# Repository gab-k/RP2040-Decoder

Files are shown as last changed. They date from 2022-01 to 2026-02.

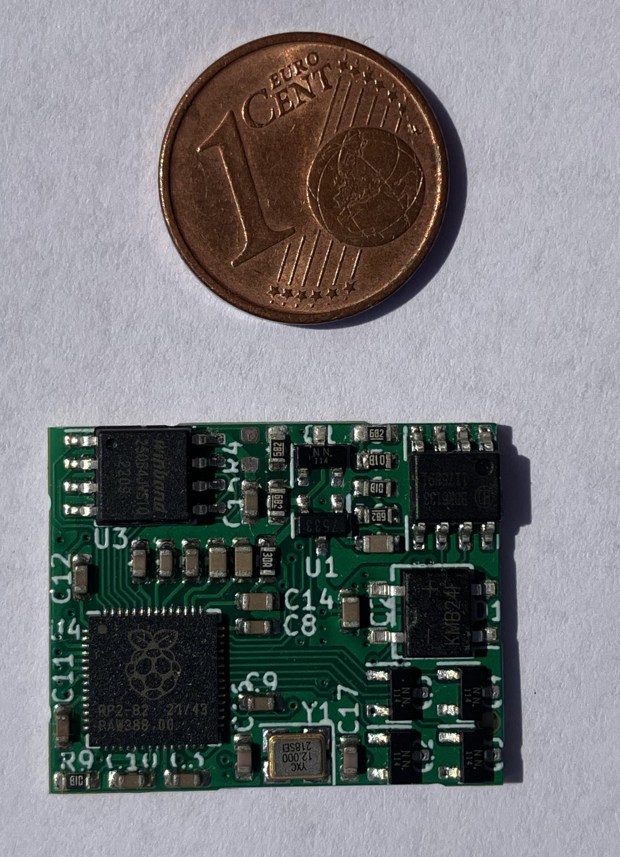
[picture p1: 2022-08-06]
docs/png/Comparison.jpg

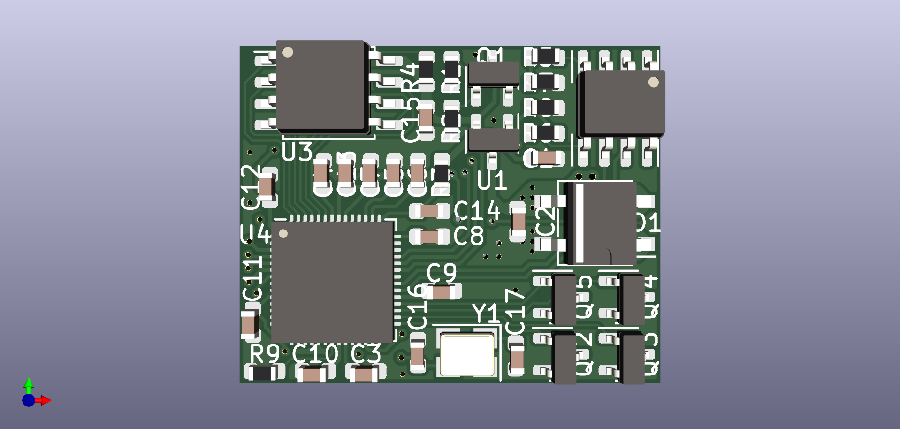
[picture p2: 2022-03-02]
docs/png/RP2040-Decoder-Rev_0_2_front.png

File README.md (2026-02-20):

# RP2040-Decoder

Designed to be a low-cost, open-source alternative to commercial DCC decoders, it utilizes the Raspberry Pi RP2040 dual-core microcontroller. The decoder features DCC protocol decoding and command interpretation alongside motor control in a compact 25x20 mm form factor.

## Key Features
*   **DCC Signal Decoding**: Interrupt-based edge detection with full packet/protocol decoding.
*   **Motor Control**: 128 speed steps with configurable acceleration/deceleration ramping and v_min/v_mid/v_max; closed-loop control for consistent motor speed under varying load conditions.
*   **Flexible I/O**: 4x transistor-switched outputs and 6x additional GPIOs; all of them PWM capable.
*   **CV Configuration**: Function mapping and programming track support.
*   **Standards Compliance**: Implements the most important NMRA (S-9.1, S-9.2.x) and RCN (210, 212, 216) DCC standards.
*   **Compact Form Factor**: 25x20 mm board size.
*   **Integrated Documentation**: Comprehensive [GitHub Pages documentation](https://gab-k.github.io/RP2040-Decoder/) covering hardware theory and software implementation.

## Architecture Overview
The system uses each of the two ARM Cortex-M0+ cores for separate tasks:

*   **Core 0: Signal Processing & Management**
    *   DCC edge detection and packet decoding.
    *   Configuration Variable (CV) management using persistent flash storage.
    *   Service Mode (Programming Track) logic and acknowledgment pulse generation.
*   **Core 1: Motion Control**
    *   **PID Controller**: A discrete-time PID motor controller implementation utilizing based on a bilinear transform formula.
    *   **Back-EMF Feedback**: ADC sampling during PWM-off cycles.
    *   **Adaptive Control**: Gain scheduling for $K_P$ and a startup controller (feed-forward) to overcome static friction.

## Hardware Revisions

### USB Version
Optimized for ease of use; supports UF2 drag-and-drop flashing and serial logging.
<div style="display: flex; gap: 10px;">
  
  
</div>

### Legacy Version
Revision without USB, one sided assembly, flashed via SWD.
<div style="display: flex; gap: 10px;">
  
  
</div>

## Getting Started

To get started, you will first need the hardware. The different options for acquiring a board are outlined [here](https://gab-k.github.io/RP2040-Decoder/sphinx/html/gs/getting_started.html#where-to-get-the-board).

For the software, you have a few options: you can either [build it from source](https://gab-k.github.io/RP2040-Decoder/sphinx/html/gs/getting_started.html#building-the-software) or use the ready-to-flash [binaries built by the CI pipeline](https://github.com/gab-k/RP2040-Decoder/releases) on each release. [Flashing the firmware](https://gab-k.github.io/RP2040-Decoder/sphinx/html/gs/getting_started.html#flashing-the-software) can be done via SWD or, if you are using the USB hardware version, simply by dragging and dropping the file using your regular file explorer.

## License

*   **Software**: MIT License
*   **Hardware**: CERN Open Hardware Licence Version 2 - Permissive

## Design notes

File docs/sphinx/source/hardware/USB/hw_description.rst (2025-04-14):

Overview
==============================

Block Diagram

   Harware block diagram

The above block diagram gives a general overview regarding the operation of components. For better illustration it has been divided into four functional blocks. Furthermore, these functional blocks can be subdivided and will be explained below.

- **Input Stage**
   - DCC Signal Level Shift
   - Bridge Rectifier & Voltage Regulator
- **Motor Driver**
   - Motor Driver
   - Back EMF measurement (ADC)
- **General Purpose**
   - GPIO
   - Auxiliary output
- **Microcontroller**
   - Flash memory
   - Crystal oscillator
   - USB Connector

Electrical Characteristics
==============================
.. table:: Electrical Characteristics & Absolute Maximum Ratings
   :widths: auto

   ========================================================  =============================  =========  =========  =====
   Parameter                                                 Symbol                         Minimum    Maximum    Unit
   ========================================================  =============================  =========  =========  =====
   Absolute max. DCC input voltage difference                V\ :sub:`DCC`\                            +24        V
   Absolute max. GPIO voltage\ :sup:`(0)`\                   V\ :sub:`PIN`\                 -0.5       3.3+0.5    V
   Input voltage high\ :sup:`(0)`\                           V\ :sub:`IH`\                  2.145      3.6        V
   Input voltage low\ :sup:`(0)`\                            V\ :sub:`IL`\                  0          1.155      V
   Total GPIO Current\ :sup:`(0)`\                           I\ :sub:`IOVDD`\                          50         mA
   Absolute max. motor output current\ :sup:`(1)`\           I\ :sub:`MOTOR`\                          2.8        A
   Absolute max. auxiliary output current \ :sup:`(2)(3)`\   I\ :sub:`AUX`\                            1.4        A
   ========================================================  =============================  =========  =========  =====

(0): According to: `RP2040 Datasheet <https://datasheets.raspberrypi.com/rp2040/rp2040-datasheet.pdf>`_ (assuming V\ :sub:`DD`\ = 3.3V)

(1): According to: `BDR6133 Datasheet <https://www.lcsc.com/datasheet/lcsc_datasheet_2409291808_Bardeen-Micro--BDR6133_C2687793.pdf>`_

(2): According to: `Si1308EDL Datasheet <https://www.vishay.com/docs/63399/si1308edl.pdf>`_ 

(3): T\ :sub:`Case`\ = 25°C, keep power dissipation, thermal resistance the corresponding temperature rise ΔT and switching losses in PWM mode in mind!

.. note:: Keep in mind that realistically these maximum ratings can't be reached in practice due to thermal limitations. For example the motor current can probably not exceed 1.5A for continuous operation.

Input Stage
==============================

Input Stage

   Input stage

D2 Rectifies the DCC square-wave into VDC, the amplitude is not critical as long as it's within the 25V limit. The rectified voltage VDC is then provided to the 3.3V voltage regulator and to the motor driver. The shottky diode D1 and the bridge rectifier D2 ensure a logical "or" linkage of the VBUS supply voltages and the DCC input voltage, meaning that the decoder can be powered either by the DCC track signal or by the VBUS supply voltage which is supplied via USB connector. 

The MOSFET on the right effectively translates the rather high DCC voltage to a suitable level for the microcontroller to process. When Q1 is turned off GPIO21 is pulled high by the RP2040 internal pull-up resistor, as soon as Q1 gets turned on (V\ :sub:`GS`\ > V\ :sub:`GS,th`\), GPIO21 gets pulled to GND potential. R1 and R2 ensure that V\ :sub:`GS`\ doesn't exceed ±12V.

Motor Driver
==============================

Motor Driver

   Motor driver

The Motor Driver is a special H-Bridge IC that is made for DC motors. To control the motor, it is necessary to measure the back-EMF voltage, which is directly related to the motor's speed. This is done by the ADC, which measures at Points ADC_EMF_A and ADC_EMF_B. The two resistors work together as a voltage divider.

Auxiliary Outputs
==============================

Auxiliary Outputs

   Auxiliary Outputs

Switching of loads can be done using four N-Channel MOSFETs (Q2 to Q5). The amount of current is somewhat dependend on either static R\ :sub:`DS(on)`\  losses and/or switching losses using PWM. They are switching on the low-side, which means the load effectively gets connected to GND potential as the transistor starts to conduct. GPIO24 - GPIO27 are used.

GPIO
==============================

To switch lighter loads, six GPIO soldering pads are connected to GPIO0 to GPIO5 pins. Although not yet set up in the software, they could be used as inputs as well (e.g. reed switch). GPIO0 and GPIO1 can also be used to facilitate stdio logging via UART, which can easily be set up in CMakeLists.txt.

Microcontroller
==============================

Microcontroller

   Microcontroller, flash memory, crystal oscillator, USB connector, ...

The Microcontroller needs a crystal oscillator for its clock. External flash memory holds the configuration variables and the program itself. The USB connector can be used to flash the software onto the decoder and also for logging via stdio (can be enabled via CMakeLists.txt). D3 is used as a status LED. R11 & C13 are used to filter ADC_AVDD (ADC Reference Voltage).

Complete Schematic
==============================

Complete Schematic

   Complete Schematic

.. _wiring_USB:

Wiring the Decoder
==============================

Wiring Diagram

    Wiring Diagram

The illustration above provides an example of a wiring configuration.
It supports the connection of up to 4 transistor-switched outputs and 6 GPIOs for lighter loads or custom applications.
When switching inductive loads, always include a free-wheeling diode to protect the circuit.

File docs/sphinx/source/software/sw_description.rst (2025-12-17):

Software Description
==============================

Overview
------------------------------

Software files high level overview:

- **core0.c / core0.h**

   - DCC package detection & decoding
   - Programming mode (Modify and read CVs on programming track)
   - ADC-Offset measurement

- **core1.c / core0.h**

   - PID motor controller
   - Back-EMF voltage measurement

- **shared.c / shared.h** (used by both cores)

   - Error handling
   - Helper functions for retrieving CV's

- **CV.h**
  
   - Default configuration variables

- **CMakeLists.txt**

   - CMake version, SDK version, C standard version
   - Board definitions
   - Compile/Build options
   - Sources files, header files
   - Debug logging configuration (via stdio using UART/USB)
   - Linked libraries

- **RP2040-Decoder-board-USB.h / RP2040-Decoder-board-Legacy.h**
   
   - Flash Size
   - Pin definitions

      - LED pin when available
      - UART_TX/UART_RX pins when used for logging
      - DCC input pin
      - Motor Control PWM pins
      - ADC pins

- **post_build.cmake**
   
   - Post build script for checking whether the size of the binary is within the limits of the flash size minus one sector (used for storing CVs).

- **pico_sdk_import.cmake**
   
   - Helps to locate and import the Pico SDK

The `Raspberry Pi Pico SDK <https://datasheets.raspberrypi.com/pico/raspberry-pi-pico-c-sdk.pdf>`_ is a dependency of the decoder software. The SDK provides abstraction to a higher level, so hopefully, in combination with the comments included in header and source files, the code is easy enough to understand.

Control Loop & Digital Controller
------------------------------------

Block Diagram - Control Loop

   Control Loop - Block diagram

The block diagram above shows the (simplified) control loop. The actual digital controller block is explained below.

The *Speed Helper* block effectively sets the setpoint of the controller according to the CV configured acceleration and deceleration rates and actual target speedstep.

For feedback the back EMF voltage *V_EMF* is measured via voltage divider and ADC. *V_EMF* is proportional to the motor speed.

While the central component is the PID controller, there is an additional block called `Feed-forward <https://en.wikipedia.org/wiki/Feed_forward_(control)>`_ that has an impact on the control output variable. The Feed-forward block adds an additional offset to the output depending on the setpoint; this is done to achieve better control. A more detailed explanation regarding Feed-forward can be found below. The speed helper block corresponds to the :c:func:`speed_helper()` function, which delays changing the setpoint according to the configured deceleration/acceleration rates.

Block Diagram - Digital Controller

   Digital Controller - Block diagram

The controller is divided into two parts, depending on whether the motor is stationary or in motion.
At all times either the startup controller or the PID controller is active.

The startup controller handles overcoming friction of the motor, and finding a base PWM level for overcoming friction.
The base PWM level is equivalent to a certain PWM duty cycle.
The base level gets saved and added to the output of the PID controller which handles motor control when the motor is in motion.
This means the actual output of the PID controller is the sum of the PID output and the base PWM level. This is referred to as the :ref:`feed forward <feed_forward>` block.
The benefit of doing this is that the PID controller does not have to work in the non linear friction region of the motor, improving control performance.

Speed Table Initialization
~~~~~~~~~~~~~~~~~~~~~~~~~~~~~~

The speed table is a crucial component of the motor control system, as it translates the 128 speed steps received from the DCC controller into specific setpoints for the PID controller. This table is initialized once at startup in the :c:func:`init_controller` function. The shape of the speed curve can be configured using three CV values: `V_min` (CV2), `V_mid` (CV6), and `V_max` (CV5).

- **V_min (CV2):** Defines the starting voltage (setpoint) for the first speed step.
- **V_mid (CV6):** Sets the voltage at the midpoint of the speed range (speed step 64).
- **V_max (CV5):** Determines the maximum voltage at the highest speed step (126).

The speed table is calculated with two linear interpolations: one from `V_min` to `V_mid` and another from `V_mid` to `V_max`. This creates a two-segment linear speed curve, which allows for a non-linear relationship between the speed step and the motor voltage. For example, you can have a gentle acceleration at low speeds and a more aggressive one at higher speeds.

The :c:func:`speed_helper` function then uses this table to gradually adjust the setpoint based on the configured acceleration and deceleration rates.

Startup Controller
~~~~~~~~~~~~~~~~~~~~~~~~~~~~~~

The startup controller is used when the motor is stationary to find the minimum PWM level required to overcome static friction. This process is not retained on a power cycle.

The initial PWM level for the startup sequence is determined as follows:

- If previous successful startup levels are saved in memory, the controller calculates their average, :math:`\bar{b}`, and sets the initial PWM level to :math:`\frac{2}{3} \cdot \bar{b}`.
- If no previous levels are saved, the ramp-up starts from a PWM level of 0.

From this starting point, the controller progressively ramps up the duty cycle until motor movement is detected. The ramp-up is not smooth but occurs in steps, with the step size determined by the maximum PWM level (which is a function of the PWM frequency).

If the PWM level reaches its maximum without motor movement, the controller reduces the starting level by half and retries, preventing excessive power to a stalled motor.

Once movement is detected (via back-EMF voltage), the current PWM `level` is saved as a new base value for future startups. This value is also multiplied by `K_FF` (from CV47) and used as the feed-forward term for the PID controller.

PID Controller
~~~~~~~~~~~~~~~~~~~~~~~~~~~~~~

PID Controller figure

   PID Controller

The block diagram above shows the PID controller in the s-domain. The derivative part contains an additional digital low-pass filter used to filter out high-frequency noise.

.. math::

   \begin{align}
   \text{Output} &= E \cdot \left(K_P + \frac{K_I}{s} + \frac{K_D \cdot s}{s \tau + 1}\right) = P + I + D \\
   P &= E \cdot K_P \\
   I &= E \cdot \frac{K_I}{s} \\
   D &= E \cdot \frac{K_D \cdot s}{s \tau + 1}
   \end{align}

With :math:`T_s` being the sampling time / controller update rate / time step of the discrete system.
And :math:`\tau` being the filter time constant of the digital filter

The continuous-time system representation can now be transformed into a discrete-time representation using `bilinear transform <https://en.wikipedia.org/wiki/Bilinear_transform>`_ :math:`s = \frac{2 \cdot (z - 1)}{T_s \cdot (z + 1)}`.

This results in the following difference equations which are then implemented in software:

.. math::
   
   \begin{align}
   p_n &= K_P \cdot e_n \\
   i_n &= 0.5 \cdot K_I \cdot \left(e_n + e_{n-1}\right) + i_{n-1} \\
   d_n &= \frac{2 K_D \cdot \left(e_n - e_{n-1}\right) + \left(2 \tau - T_s\right) \cdot d_{n-1}}{2 \tau + T_s} \\
   \text{output}_n &= p_n + i_n + d_n
   \end{align}

.. note::
   - Instead of using the derivative of error, the derivative on measurement is used. This is done to prevent a high derivative part in the event of a large change in setpoint.
   - The previously explained base PWM is added to the actual output as well, meaning the formula above only shows the actual PID control part without feed forward. 

Gain Scheduling
^^^^^^^^^^^^^^^^^^^^

Gain Scheduling figure
   
   Gain Scheduling

Another aspect to consider is the implementation of `gain scheduling <https://en.wikipedia.org/wiki/Gain_scheduling>`_. K\ :sub:`P` is a function of the current setpoint. Often it is favorable to have a higher proportional gain K\ :sub:`P` for slow speeds, achieving better control results. The illustration above shows the default setting for K\ :sub:`P`. CV_54 & CV_55 are used to set K\ :sub:`P` @ x\ :sub:`0`, CV_56 & CV_57 for K\ :sub:`P` @ x\ :sub:`1`, and CV_58 & CV_59 for K\ :sub:`P` @ x\ :sub:`2`. Additionally, CV_60 is used to shift x\ :sub:`1` from the leftmost point (0% = 0/255) to the rightmost point (100% = 255/255).

The :c:func:`get_kp()` function implements this gain scheduling. It calculates the proportional gain `K_p` based on the current setpoint `sp`. The function uses two different linear equations to determine `K_p`, depending on whether the setpoint is above or below the `k_p_x_1` threshold. This creates a piecewise linear function for `K_p`, allowing for different gain characteristics at different speed ranges.

The parameters for these linear equations (`k_p_m_1`, `k_p_m_2`, `k_p_y_0`, `k_p_y_1`) are pre-calculated in the :c:func:`init_controller` function based on the corresponding CV values.

.. _feed_forward:

Feed-forward
^^^^^^^^^^^^^^^^^^

As previously mentioned, to achieve better control, `Feed-forward <https://en.wikipedia.org/wiki/Feed_forward_(control)>`_ is used.
In essence this means that the output of the PID controller is not only the sum of the proportional, integral, and derivative parts, but also the base PWM level.
The base PWM level is set by the startup controller and is the PWM level at which the motor starts moving.

Speed Helper
^^^^^^^^^^^^^^^^^^

The :c:func:`speed_helper` function is responsible for implementing smooth acceleration and deceleration. It is called by a repeating timer, with the interval configured by CV175. This function acts as a temporal filter for the speed setpoint.

Instead of instantly changing the motor's setpoint to the new target speed step, the :c:func:`speed_helper` function gradually increments or decrements the current setpoint based on the acceleration (CV3) and deceleration (CV4) rates. These CVs determine how many calls to :c:func:`speed_helper` are needed for a single speed step change. For example, if the acceleration rate is set to 5, the :c:func:`speed_helper` must be called 5 times before the setpoint is incremented to the next speed step. This creates a time-based acceleration/deceleration curve.

The function also handles direction changes. If a direction change is detected, it will immediately jump to the new target speed without any delay, ensuring a responsive change in direction.

Back-EMF voltage measurement
~~~~~~~~~~~~~~~~~~~~~~~~~~~~~~

To provide a feedback signal proportional to the motor speed, the ADC is used to measure the `Back-EMF voltage <https://en.wikipedia.org/wiki/Counter-electromotive_force>`_. The measurement works by setting the PWM duty cycle to 0%, waiting for a certain delay time (CV_62), and then measuring x times (x = CV_61). The ADC input channel is selected based on the motor's direction (forward or reverse). While measuring, the array with measurement values is sorted using insertion sort. Afterwards, y elements (y = CV_63) from the left (lowest values) and z elements (z = CV_64) from the right (highest values) will be dismissed to mitigate the impact of potential outliers in measurement. The average value of the remaining values will be computed and fed back into the control algorithm. Considering default settings (100us delay, 100 samples, ~2µs sampling time), the complete measurement run, including averaging, takes about 0.3ms to 0.35ms, which effectively reduces the maximum possible duty cycle to about 93% to 94%.

DCC signal decoding
------------------------------

The detection of the DCC signal works by looking at every rising and falling edge and calculating the time between them. When the time between rising and falling edge is greater than 87μs, then this is equivalent to "0"; otherwise, "1". This value then gets shifted into a 64-Bit variable.

Decoding is done after every falling edge. It starts with an error detection, which, when not passed, dismisses the received command. Then the address will be decoded and compared to the address stored in the configuration. If the address matches, the command/instruction will be decoded.

Only a few instructions are currently implemented; only 128 speed step instructions are supported.

**Implemented instructions:**

- ``0011-1111`` - (128 Speed Step Control) - 2 Byte length
- ``10XX-XXXX`` - (Function Group Instruction) (F0 - F12)
- ``110X-XXXX`` - Expansion Instruction  (F13 - F31)

All DCC instructions can be found in Section 9.2, 9.2.1, and 9.2.1.1 of the `NMRA Communications Standard <https://www.nmra.org/index-nmra-standards-and-recommended-practices>`_.

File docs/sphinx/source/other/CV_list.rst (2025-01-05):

Configuration Variables (CV)
============================

.. note:: 
   
   - ``CV.h`` contains default values for every CV. When your board is still "factory new" these values are automatically written into flash. ``CV_65 == 255`` indicates a factory condition and resets all CVs to default.
   
   - Index 0 in the CV array corresponds with ``CV_1``, index 1 corresponds with ``CV_2`` and so forth.

Reset all CVs
------------------------

To reset all CVs to default, a value of ``8`` can be written to ``CV8``. Alternatively write a value of ``255`` to ``CV_65`` this will also reset all CVs to default, but only after power cycling the decoder.

Speed step configuration
------------------------

Speed Table

   Speed Table

* :math:`v_{min} = CV_{2}`
* :math:`v_{mid} = 16 \cdot CV_{6}`
* :math:`v_{max} = 16 \cdot CV_{5}`

The figure above shows how the speed steps can be configured using the corresponding CVs. The red * represents :math:`v_{min}` which is always at speed step 1, the green * shows :math:`v_{mid}` at speed step 63, and the blue * shows :math:`v_{max}` at speed step 126.

CV List
-------

:math:`CV_{1}` - Basic address
~~~~~~~~~~~~~~~~~~~~~~~~~~~~~~~~~~~~~~~~~~~~~~~~~~~~~~~~~~~~~~~~~~~~~~~~~~~~
Short DCC address

:math:`CV_{2}` - :math:`v_{min}`
~~~~~~~~~~~~~~~~~~~~~~~~~~~~~~~~~~~~~~~~~~~~~~~~~~~~~~~~~~~~~~~~~~~~~~~~~~~~
Min motor voltage/speed is: :math:`v_{min} = CV_{2}`

:math:`CV_{3}` - Acceleration rate
~~~~~~~~~~~~~~~~~~~~~~~~~~~~~~~~~~~~~~~~~~~~~~~~~~~~~~~~~~~~~~~~~~~~~~~~~~~~
The time for one discrete acceleration time step can be calculated as :math:`CV_{3} \cdot CV_{175}`.

.. note:: Base speed steps are always 128/126 steps.

:math:`CV_{4}` - Deceleration rate
~~~~~~~~~~~~~~~~~~~~~~~~~~~~~~~~~~~~~~~~~~~~~~~~~~~~~~~~~~~~~~~~~~~~~~~~~~~~
The time for one discrete deceleration time step can be calculated as :math:`CV_{4} \cdot CV_{175}`.

.. note:: Base speed steps are always 128/126 steps.

:math:`CV_{5}` - :math:`v_{max}`
~~~~~~~~~~~~~~~~~~~~~~~~~~~~~~~~~~~~~~~~~~~~~~~~~~~~~~~~~~~~~~~~~~~~~~~~~~~~
Max motor voltage/speed is calculated as: :math:`v_{max} = 16 \cdot CV_{5}`

:math:`CV_{6}` - :math:`v_{mid}`
~~~~~~~~~~~~~~~~~~~~~~~~~~~~~~~~~~~~~~~~~~~~~~~~~~~~~~~~~~~~~~~~~~~~~~~~~~~~
Mid motor voltage/speed is calculated as: :math:`v_{mid} = 16 \cdot CV_{6}`

:math:`CV_{7}` - Version No. (Read-Only)
~~~~~~~~~~~~~~~~~~~~~~~~~~~~~~~~~~~~~~~~~~~~~~~~~~~~~~~~~~~~~~~~~~~~~~~~~~~~
Writing a value of ``7`` triggers an ADC offset adjustment.

:math:`CV_{8}` - Manufacturer (Read-Only)
~~~~~~~~~~~~~~~~~~~~~~~~~~~~~~~~~~~~~~~~~~~~~~~~~~~~~~~~~~~~~~~~~~~~~~~~~~~~
Default = ``13`` = Public Domain & Do-It-Yourself Decoders

Even though :math:`CV_{8}` is defined as a Read-only CV, writing a value of ``8`` resets all CV values to the default values in ``CV.h``.

:math:`CV_{9}` - Motor PWM Frequency
~~~~~~~~~~~~~~~~~~~~~~~~~~~~~~~~~~~~~~~~~~~~~~~~~~~~~~~~~~~~~~~~~~~~~~~~~~~~
:math:`f_{PWM_{MOTOR}} = (CV_9 \cdot 100 + 10000) \, Hz`

:math:`CV_{11}` - Packet timeout
~~~~~~~~~~~~~~~~~~~~~~~~~~~~~~~~~~~~~~~~~~~~~~~~~~~~~~~~~~~~~~~~~~~~~~~~~~~~
If no package is received for :math:`x = CV_{11}` seconds the decoder will automatically stop the motor (Emergency Stop).

:math:`CV_{12}` - Permitted operating modes
~~~~~~~~~~~~~~~~~~~~~~~~~~~~~~~~~~~~~~~~~~~~~~~~~~~~~~~~~~~~~~~~~~~~~~~~~~~~
Currently, DCC Digital mode is the only supported mode.

:math:`CV_{17}` & :math:`CV_{18}` - 14-Bit extended/long address
~~~~~~~~~~~~~~~~~~~~~~~~~~~~~~~~~~~~~~~~~~~~~~~~~~~~~~~~~~~~~~~~~~~~~~~~~~~~
Address is only used if bit5 of :math:`CV_{29}` has a value of ``1``.

Long Address

Bit15 and bit14 which correspond to bit7 and bit6 of :math:`CV_{17}` are always ``1``. :math:`CV_{17} = 192` & :math:`CV_{18} = 0` is also not a valid address.
Otherwise, the valid value range of :math:`CV_{17}` ranges from ``192`` to ``231`` and ``0`` to ``255`` for :math:`CV_{18}` respectively.

:math:`CV_{29}` - Decoder Configuration
~~~~~~~~~~~~~~~~~~~~~~~~~~~~~~~~~~~~~~~~~~~~~~~~~~~~~~~~~~~~~~~~~~~~~~~~~~~~
Bit0 is can be used to reverse motor direction, i.e., ``0`` = normal, ``1`` = reverse.  
Bit5 switches between basic and extended addressing modes, i.e., ``0`` = basic address, ``1`` = extended address.
The other 6 bits are currently not in use and therefore irrelevant.

:math:`CV_{31}` & :math:`CV_{32}` - Extended CV pointer (Read-Only)
~~~~~~~~~~~~~~~~~~~~~~~~~~~~~~~~~~~~~~~~~~~~~~~~~~~~~~~~~~~~~~~~~~~~~~~~~~~~
Not in use.

:math:`CV_{116}` to :math:`CV_{171}` - PWM Slice configuration
~~~~~~~~~~~~~~~~~~~~~~~~~~~~~~~~~~~~~~~~~~~~~~~~~~~~~~~~~~~~~~~~~~~~~~~~~~~~
GPIO Slices

Every slice controls two independent output channels, duty cycle from 0% to 100% inclusive, and can be configured with several parameters:

* Wrap (16Bit): Sets the slice time period of x cycles - effectively determining the frequency
* Clock Divider: Additional clock divider
* Level Channel A / Level Channel B (16Bit each): Determining how many of the x cycles the signal is at a high level - effectively determining the duty cycle

To see which CVs correspond to which slice and channel, it is advisable to use ``CV.h`` as a reference.

The PWM frequency is calculated as follows: :math:`f_{PWM} = \frac{125 \, \text{MHz}}{(CV_{\text{clk_div}} + 1) \cdot (CV_{\text{wrap}} + 1)}`

The duty-cycle can be calculated as follows: :math:`D = \frac{CV_{\text{Level}}}{CV_{\text{wrap}} + 1}`

A more detailed explanation regarding PWM can be found in the `RP2040-Datasheet - Chapter 4.5 <https://datasheets.raspberrypi.com/rp2040/rp2040-datasheet.pdf>`_.

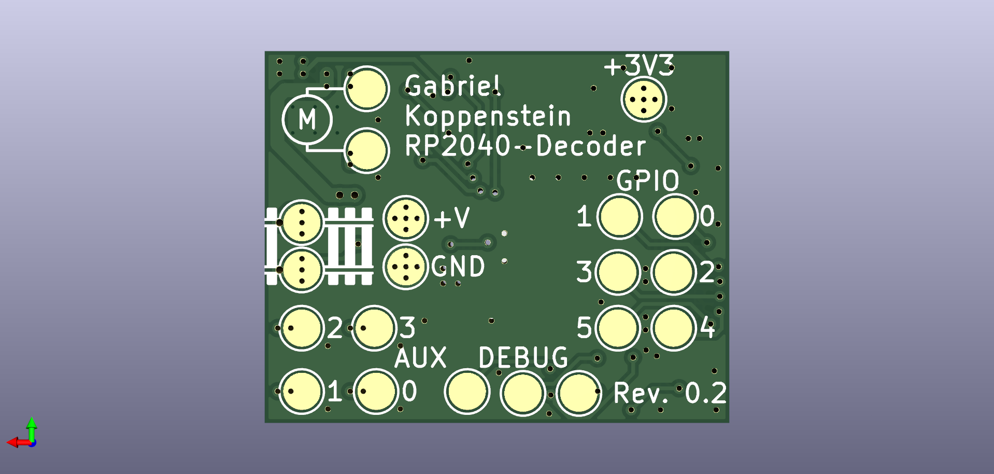
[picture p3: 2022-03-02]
docs/png/RP2040-Decoder-Rev_0_2_back.png

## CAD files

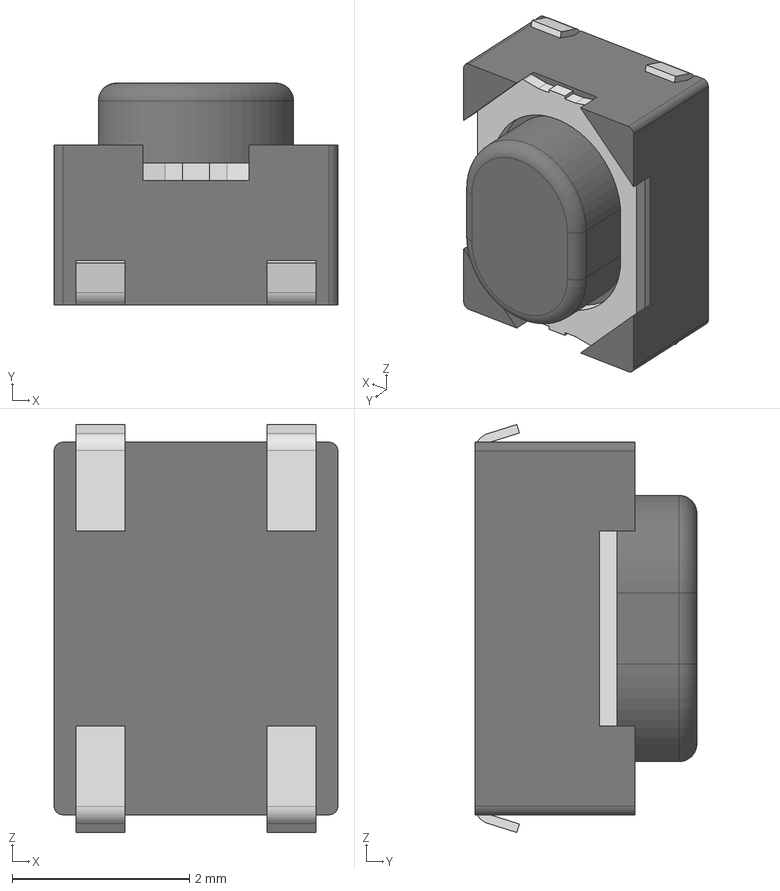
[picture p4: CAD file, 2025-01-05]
KiCad/USB/434133025816.stp
3.20 x 2.50 x 4.60 mm
Frame
Cover
Stem
Terminal x 4

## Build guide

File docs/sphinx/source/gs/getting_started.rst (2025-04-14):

Getting started
==================================

1. Where to get the board?
----------------------------------

You can choose any PCB manufacturer. The PCB is designed to fit within the capabilities and constraints of JLCPCB.com.
You have 3 options for board assembly from the most difficult to the easiest:

1. You can assemble the board yourself, but it's best not to do so if you're not familiar with soldering small components. You order the board with the necessary parts and solder the parts. The parts are available at LCSC.com, they supply parts to JLCPCB.com.
2. Order the PCB from any PCB manufacturer and have only the top side assembled. This way You have to separately order the parts for the bottom part from LCSC.com (or any other supplier) and solder just the bottom part yourself. Soldering the back of the PCB by hand is not too difficult.
3. Alternatively, you can order the board fully assembled both on the top and bottom side. This is the easiest, but the most expensive solution.

2. Production files?
----------------------------------
The latest release includes the production files for JLCPCB, which includes the Gerber files, BOM, and Pick and Place files. You can find the latest release `here <https://github.com/gab-k/RP2040-Decoder/releases>`_.

In order to manually export the production files (Gerber/BOM/Pick and Place), you need `KiCad <https://www.kicad.org/download/>`_ which is open source.
In case you are ordering from JLCPCB it is recommended to use the `Fabrication-Toolkit KiCad plugin by bennymeg <https://github.com/bennymeg/Fabrication-Toolkit>`_

.. _building_the_software:

3. Building the software
----------------------------------

If you got a RP2040-Decoder with USB the easiest way to get the RP2040-Decoder up and running is to just use the precompiled .uf2 file in the latest `release <https://github.com/gab-k/RP2040-Decoder/releases>`_ and skip to :ref:`flashing_the_software`.

However sometimes you might want to build by yourself, be it for debugging or to make your own modifications to the source code.
The easiest way to do this is to just use `Visual Studio Code <https://code.visualstudio.com/>`_ and the `Raspberry Pi Pico extension <https://marketplace.visualstudio.com/items?itemName=raspberry-pi.raspberry-pi-pico>`_. 
The `official documentation <https://datasheets.raspberrypi.com/pico/getting-started-with-pico.pdf#vscode-extension>`_ of the Pi Pico does a great job of explaining this in detail.

.. note::
   - Make sure to choose the correct board definition file in your CMakeLists.txt file ``RP2040-Decoder-board-USB`` for the USB Hardware or ``RP2040-Decoder-board-Legacy`` for the old legacy version without usb.
   - In VSCode open the "Software" subdirectory for the extension to detect you project automatically.

.. _flashing_the_software:

4. Flashing the software
----------------------------------

For RP2040-Decoders with USB there is two ways of flashing the software:

1. Flashing via USB using the .uf2 file by copying it with your preferred file explorer. 
2. Using Serial Wire Debug (SWD)

   2.1. Using another RP2040/RP2350-based board with `debugprobe software <https://github.com/raspberrypi/debugprobe>`_ on it. (Could be the RP2040-Decoder itself)

   2.2. Using any other supported SWD debug interface

For RP2040-Decoders without USB the only way of flashing the software is via SWD

4.1. Flashing the software via .uf2 file
^^^^^^^^^^^^^^^^^^^^^^^^^^^^^^^^^^^^^^^^^^^^^^^^^^^^^^^^^^^^^^^^^
When first plugged in the RP2040 boots into Mass Storage Device mode. To flash the software, you need to drag the '.uf2' file onto the disk using any file explorer.
This will write the file to the Flash and restart the RP2040.
In case you want to repeat the flashing process, hold the button SW1 while re-plugging the decoder into your computer. The decoder should now show as a Mass Storage Device again.
This procedure is also described in the `Raspberry Pi Pico Datasheet Chapter 4.1 <https://datasheets.raspberrypi.com/pico/pico-datasheet.pdf#_programming_the_flash>`_

.. _flashing_the_software_swd:

4.2. Flashing the software via SWD
^^^^^^^^^^^^^^^^^^^^^^^^^^^^^^^^^^^^^^^^^^^^^^^^^^^^^^^^^^^^^^^^^
Flashing via SWD is a little more complicated but also comes with great advantages in terms of debugging.
The book on `Getting started with Raspberry Pi Pico-series <https://datasheets.raspberrypi.com/pico/getting-started-with-pico.pdf>`_ does a great job of explaining how debugging works.
As already suggested in :ref:`building_the_software` it is recommended to use the `Visual Studio Code Extension <https://datasheets.raspberrypi.com/pico/getting-started-with-pico.pdf#vscode-extension>`_.
The most relevant sections in the book are `Chapter 4.3. Debug <https://datasheets.raspberrypi.com/pico/getting-started-with-pico.pdf#_debug>`_ and `Appendix A: Debugprobe <https://datasheets.raspberrypi.com/pico/getting-started-with-pico.pdf#debugprobe_section>`_

5. Wiring
----------------------------------

| Please refer to the hardware section for your board:
| :ref:`Wiring USB Hardware Revision <wiring_USB>`
| :ref:`Wiring Legacy Hardware Revision <wiring_Legacy>`

6. Resolving issues
----------------------------------

If the decoder is not working as expected:

1. Follow the `Troubleshooting instructions <https://github.com/gab-k/RP2040-Decoder/wiki/Troubleshooting>`_
2. If you still have trouble, create a new `discussion <https://github.com/gab-k/RP2040-Decoder/discussions>`_ or `issue <https://github.com/gab-k/RP2040-Decoder/issues>`_ and describe your question/issue.

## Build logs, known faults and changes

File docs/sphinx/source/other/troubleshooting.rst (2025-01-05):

Troubleshooting
================

To narrow down the issue when your decoder is not working as expected, you can do the following (in no particular order):

Enable logging and or debug via SWD
------------------------------------
Log messages can be enabled and output via either UART or USB please see :ref:`logging` for details.
For more advanced users it might also be beneficial to :ref:`debug with SWD <debugging_via_swd>`

Checking the power supply:
--------------------------------------

* **+3V3 to GND** should be 3.3V ± 1%
* **VDC/+V to GND** should be somewhere in the range of at least 6V to 23V depending on your track voltage.

If you don't measure the correct voltages, try to `measure your track voltage <https://dccwiki.com/Measuring_Track_Voltage>`_

Check your motor:
-----------------

Desolder your motor and try the motor with an appropriate power supply and DC voltage, to check if the motor is working or not.

CV Reset:
------------

Try to reset the decoder by writing a value of ``8`` to ``CV8`` (beware, this will reset the complete CV memory!)

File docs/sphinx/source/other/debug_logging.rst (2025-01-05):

Debugging and Logging
==================================

For logging and debugging you have to build the software yourself. This is explained here: :ref:`building_the_software`

.. _debugging_via_swd:

Debugging via SWD
----------------------------------
Please refer to :ref:`flashing_the_software_swd`.

.. _logging:

Logging
----------------------------------

Logging can be enabled in ``CMakeLists.txt``, and is available with two interfaces:

    - Logging via UART RX/TX pins (GPIO0/GPIO1 by default)
    - Logging via USB CDC/ACM

Additionally you can make the decoder wait for input via serial port by setting LOG_WAIT to 1. For more details please see comments inside ``CMakeLists.txt``.

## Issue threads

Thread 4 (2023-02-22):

Not really an issue, but...

hinds44, 2023-02-22:
Raspberry Pi themselves have created a Minimal RP2040 board using KiCAD

I forked today to start working on the PCB and align its design with R Pi's own.

Closed 2023-07-15.

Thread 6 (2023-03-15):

Files for ordering

questor, 2023-03-15:
Hi!
I really love your idea of a homebrewn decoder, but I'm more a software guy and have issues producing the files needed to order pcb's (I've tried jlcpcb). Producing the gerber files worked, but creating the placement files showed that 1) I have issues selecting the right parts because of footprint and 2) one component was not available (U3 in the right footprint format) and 3) the placement was very off (I think because of negativ Y position, but I'm not really sure because I also had to mess a lot with the files to get the webservice accepting the files).
In short, I really want to have some decoders to test them, but I feel uneasy with no prepared files which are known to work... Getting the files per email would also be fine, you can find my email address on my website which is linked in my github profile..

Thanks for this great project!
-Kai

gab-k, 2023-03-15:
Hey Kai,
Thank you for the interest. There are a few things to note about production files for JLCPCB. The following links should contain all the necessary information:
https://support.jlcpcb.com/article/194-how-to-generate-gerber-and-drill-files-in-kicad-6
https://support.jlcpcb.com/article/84-how-to-generate-the-bom-and-centroid-file-from-kicad

I have also attached the production files.
[Production_Files.zip](https://github.com/gab-k/RP2040-Decoder/files/10984695/Production_Files.zip)

You may need to rotate some components in JLCPCB's component placement preview. When choosing capacitors, also consider the maximum voltages.

Gabriel

questor, 2023-03-16:
great, thanks for all the infos! will try tonight to order some boards...

questor, 2023-03-17:
the pictures really helped me ordering some boards to test them, many many thanks for providing them! one feedback I got: even though the placements were shown correctly in the web-preview it needed to be corrected manually by an engineer on their side, not sure why. and they replaced the D1 by "FUXINSEMI KMB24F".

An idea for improvement would be to integrate a way over custom commands to be able to update the software on the decoder without opening the train via the programming track and special custom software running on the dcc-ex.

I owe you one or two beers for the project and your help! If you're around Karlsruhe drop me a note ;)

questor, 2023-03-17:
is there a possibility to get more switches by using more gpios easily?

gab-k, 2023-03-17:
I don't quite understand, the software can only be [changed or programmed via serial wire debug.](https://github.com/gab-k/RP2040-Decoder/wiki/Getting-started#3-building-and-flashing) What do you mean with the special custom software that is on the dcc-ex? Do you perhaps mean the configuration variables or are you talking about the software as a whole? With regard to the switches, it is possible to implement additional switches, but the PCB would have to be modified for this, since not all pins are brought out on a pad.

questor, 2023-03-17:
I was thinking that for the very first time you still need the serial wire debug, but afterwars the software can flash itself via a special protocol implemented in this decoder and for example on the dcc-ex as this is also opensource. I assume currently to apply an updated firmware you need to open the train and solder something to be able to use the serial wire debug.

let's wait until I get my first batch of decoders to find out if that is really needed or not.

questor, 2023-03-27:
Received my batch, not tested yet. Two points: when looking at the schematics the board should work with direct current as well as with alternating, right? If yes, a comment would be good that OLD transformators should NOT be used as the direction switch done with old transformators can go up to 32V and from looking at your wiki your decoder is "only" save up to 25V or am I missing something?

gab-k, 2023-03-27:
The power supply as such works with both AC and DC voltage, but pure DC voltage or e.g. 50Hz AC voltage from a Märklin transformer is of little use because of course no information (e.g. driving commands) can be transmitted. The physical properties of the DCC signal are explained quite well [here ](https://www.opendcc.de/info/dcc/dcc.html)in German. As far as the maximum input voltages are concerned, the motor driver is the limiting factor. The absolute maximum voltage on the track should not exceed 27V in terms of amplitude, since the motor driver has an absolute maximum input voltage of 26V, but the bridge rectifier still has a drop of approx. 1V. You also have to keep the maximum capacitor voltage in mind. With the 10uF capacitors I suggested, the maximum voltage is 25V.

questor, 2023-03-27:
okay, silly me, thanks for the clarification. still a lot to learn with all the new stuff (at least for me). thanks!
small hints for documentation, the pico-sdk is moved to a different location: https://github.com/raspberrypi/pico-setup-windows  and the probe-utility is also moved to an own space where already compiled binaries can be downloaded: https://github.com/raspberrypi/picoprobe/releases/tag/picoprobe-cmsis-v1.02

questor, 2023-03-27:
another update: openocd does not need anymore picoprobe.cfg: https://forums.raspberrypi.com/viewtopic.php?t=348242

questor, 2023-03-28:
I used "openocd -f interface/cmsis-dap.cfg -f target/rp2040.cfg -c "program RP2040-decoder.elf verify reset exit""  and programming and verify SEEMS to work (reported back successful). But currently I can't test the decoder as some basic stuff is still missing (I'm fighting with ArduinoIDE for the dccex command station, but that's not related to this project)

questor, 2023-04-16:
Okay, I've got my missing components, but so far no luck with getting it to work. How can I read the debug-uart output from the decoder? Is it save to connect the tracks AND the serial wire debug interface to find out what/if the decoder is doing something or if it's missing informations because my setup if faulty (for background: when I connected the motor the first time at the first startup the train moved, but the motor driver ic got really hot, not sure why. and now after a day where I checked the motor and other stuff nothing is happening, not sure if the chip got too hot and died, if power is missing or what is going on)

gab-k, 2023-04-16:
I presume you successfully programmed the decoder via openocd? From your description it is kind of hard to tell what's happening. First of all it would be helpful to check the +V and 3V3 voltages. You can also connect a relatively low resistance resistor as a load for the motor driver and try to read CVs on the programming track (The resistor is needed as it provides an acknowledgment for the central as to which bits are set). Another thing you can try, is to check the GPIO by mapping one of the functions to correspond with one GPIO pin via the table "CV.h".
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
gab-k, 2023-05-11:
> printf debugging is fine, I knew about SWD debugging but for now I prefer printfs...

However you prefer, keep in mind the time it takes to execute printf regarding time critical tasks like the motor controller. In this case there shouldn't be a problem with that.

> I don't have another motor I can test with, at least no one from a locomotive... can I somehow test if the motor is working by desoldering the decoder and applying dc directly to the motor?

Yes, that's a good idea.

> when I do the measurements and apply manual rotation to the motor the measurements do NOT change, is that normal?

Whilst that will generate a voltage, it might not be in the moment the ADC samples it.

gab-k, 2023-05-11:
> does it make sense to replace the motor by a 100ohm resistor and do the measurements to find out if that works?

No, the measurement works by measuring the back-EMF voltage of the motor.

> and in addition I plan to replace the decoder by another one, my only concern is if the first one was damaged somehow, how can I be sure that the second one is not damaged.... (of course I will apply directly the printf-version to directly see the first startup and get measurements.

I'm gonna write you a test function later, I'm on my phone ATM.

> (does it make sense here to use the 100ohm resistor just to check if everything works as expected?)

Same as above, the resistor lacks physical properties, i only recommended it for testing the CV reading functionality.

gab-k, 2023-05-11:
Try this [test function](https://pastebin.com/Fzj8yR2R) calling it somewhere about [line 552 in core0.c ](https://github.com/gab-k/RP2040-Decoder/blob/main/core0.c#L552) should be fine i think. The expected ADC values should be a rather high values depending on track voltage a bit of course.

gab-k, 2023-05-19:
> edit: after opening the motor, checking the rotor and closing the motor again the motor works with dc applied directly. will check more, sorry for all the mess :/

Don't worry

> are you interested in my debug logging (it's compiled out when disabled, but can easily be enabled. I could clean up a bit and make a pull request if you want to have the logging stuff. I will do a wiki-page how to debug.

Yes that is a very good idea.

Can i contact you some way via email, perhaps the one on your website?

questor, 2023-05-19:
you're more than welcome to write an email: http://www.unseen-academy.de/legal.html   german is fine ;)

will prepare some more commits with documentation about debugging...

questor, 2023-06-01:
have you written an email? I have received nothing so far?

chenhongmai, 2023-06-19:
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
Hi @questor , I am also having the problem with motor keep turning with 15.8V and it is not controlled by the DCC command station. I am using the ESU decoder tester PCB (with a motor and some lights) and I could verify that the motor is in good condition. Do you have any thoughts on this?

questor, 2023-06-20:
I've an open pull-request with logging enabled in the decoder, you have to compile my branch, attach the flashing-rp2040-board without the VCC from the flashing-board (it's powered by the tracks, for reference from Gabriel:  "Wether it is safe to connect both SWD and supply power using the tracks depends on your setup. What i mean by that is, you would have to keep in mind that if for example you are using the dccex command station and it is connected to your PC that is also connected to your programmer all of those ground potentials are tied together. If you now tie GND of the decoder together with the GND potential of your programmer / dcc-ex / PC you are effectively bridging one of the diodes in the bridge rectifier as the GND potential of the Decoder is actually one diode voltage drop (~0.7V) lower than the GND potential of your programmer / dcc-ex / PC GND. Although i would not recommend it, it should be alright in most cases you of course shouldn't supply power from both the programmer and the tracks, as in only tieing GND to GND, GPIO2 to SWCLK, GPIO3 to SWDIO and not connecting VBUS to your decoder.").
I don't fully understand the issue, but it worked for me to connect the tracks AND the flashing-board without VBUS and I was able to receive debug printfs I've added (you have to enable compile-time switches in my repo to enable printfs!).

In the end I think what happened on my side: I have issues with the motor which resulted in corrupt measurements with the result of a really strange behaving decoder.

Another tip: to check basic connectivity between your decoder and the command station you can desolder the motor and replace it by a resistor of ~100ohms to be able to check the connection between commandstation and the decoder (reading and writing CVs should work!).

Closed 2023-07-17.

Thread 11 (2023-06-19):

Motor not controlled

chenhongmai, 2023-06-19:
Hi Gab-k,

I have the PCB made by JLC and soldered with components. I could verify that the function works partially as the lights are working corresponding to the CV.h. However, after the initial tuning the motor is running at full speed and not controlled (as long as the decoder is connected to the track) and the motor IC and bridge gets extremely hot...(very similar to the other post...)

We adjust to CV52/53=50 but the motor is running slow, still not controlled by the DCC center.

I also tried to solder a 1210 resistor to the motor ports as a load, but probably due to previous problems with motor running at full speed it won't work (very hot...)

Another functionality issue:
We wrote CV257=1, to map GPIO24 for front headlight. It does not work. With the CV261=2 the rear headlight works.

Our test equipment:
ESU lokprogrammer
ESU decoder tester

What is your thoughts on the problem?
Thanks for your help.

gab-k, 2023-06-19:
Try Re-running the motor calibration after you are certain that your motor works, perhaps by supplying it with a DC voltage directly.
Regarding the function mapping make sure your light works.

chenhongmai, 2023-06-26:
Hi Gab,

Thank you for your help.
Another question, is POM programming on main mode possible?
Thanks.

gab-k, 2023-06-26:
Certainly possible but not currently implemented in Software.

chenhongmai, 2023-07-07:
> Try Re-running the motor calibration after you are certain that your motor works, perhaps by supplying it with a DC voltage directly. Regarding the function mapping make sure your light works.

Hi,

I made a test PCB to test all the functions, and I tried to map F0 forward to the LED and is still not working. But the exact same LED works for the other channels. I think there might be a bug somewhere in the directional light outputs.

In regards to the motor control, after tuning, the motor is still running full speed without being controlled.
Our test equipment:
ESU lokprogrammer
ESU decoder tester

We tried to re-tune the motor but it does not work, still running full speed.
The test equipments are all good.

Thanks for helping...still try to see why this happened. Hopefully these information helps for debugging.

gab-k, 2023-07-15:
> In regards to the motor control, after tuning, the motor is still running full speed without being controlled. Our test equipment: ESU lokprogrammer ESU decoder tester

I just merged a pull request kindly provided by questor, it adds functionality for logging various parameters using uart or usb, this might help you troubleshoot. If the motor runs at full speed, this indicates that the I component of the PID controller is rising too high or that the calibration is incorrect.

> I made a test PCB to test all the functions, and I tried to map F0 forward to the LED and is still not working. But the exact same LED works for the other channels. I think there might be a bug somewhere in the directional light outputs.

Unfortunately I cannot really help you with this issue at the moment as I lack the time to do so, however I encourage you to resolve the issue on your own, as it can't be all too complicated considering it involves only toggling a GPIO pin.

Closed 2023-10-28.

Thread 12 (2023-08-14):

schema kicad

LaurentDelaon, 2023-08-14:
on your Schema R4 is Do Not Fit so you don't put it ?

gab-k, 2023-08-14:
You are correct, R4 is optional. Some Flash Memory IC's require it, so the pad is there but not populated in case you are using the W25Q64JVSSIQ

Closed 2023-10-28.

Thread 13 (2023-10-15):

Incorrect parameter passed

RadarWizard, 2023-10-15:
I'm developing a STM32L151 based dcc decoder and was looking at your code as a possible starting point. Your project looks great and the pid control is a bit beyond my understanding. However, I did notice a slight error on the line below which you may like to correct.

https://github.com/gab-k/RP2040-Decoder/blob/10fbcb5815ce81fd1c1bedcceed3cfd5c92fd319/core1.c#L179

I believe it should have passed msr_delay_in_us not msr_total_iterations. It works at the moment because these two numbers have the  same value of 100.

gab-k, 2023-10-15:
You are correct that line is incorrect. Thanks for bringing it to my attention.

Closed 2023-10-28.

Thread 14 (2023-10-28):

Add USB-C connector

chatelao, 2023-10-28:
I love this project and think it has the potential to shake the Model-Railroad community.

The great thing about the RP2040 is the included permanent ROM uf2 Bootloader. Yes, adding a USB-C interface will cost some realestate, BUT would lower the bar for developers signifcantly, removing the need to understand SWD programming at all.

I think, as soon as the Software compiles in a Ardunino environment, the support of entry enthusiast will explode.

The "adafruit QT RP2040" may be a good source to copy-paste ideas?
- https://learn.adafruit.com/assets/101678

gab-k, 2023-10-28:
I agree and also thought about adding the USB connector before. If I have the time I might change the PCB with an optional USB connector on the back side in the future.

chatelao, 2023-10-29:
It would be great - I tried to do it myself, but failed misarably.

I would like to try to add a Märklin (MM2) supported firmware version.

btw: Reading and Writing a config file with all CVs and Parameters over a USB-C  could greatly simplyfing the process of decoder setup. Even sound files in a microcontroller compatible format could be added "drag n drop".

chatelao, 2025-09-13:
Oh, die USB Version sieht sehr schön aus. Ich hab mir überlegt, ob man mit senkrechten Buchsen etwas weniger Platz auf der Platine bräuchte.

Closed 2024-05-05.

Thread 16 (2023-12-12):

nmake not found

Space-Farmer, 2023-12-12:
Hello,

I have an issue during build process.
I got the following error:

PS C:\Users\danie\Documents\Pico-v1.5.1\RP2040-Decoder\build> cmake -G "NMake Makefiles" ..
Using PICO_SDK_PATH from environment ('C:\Program Files\Raspberry Pi\Pico SDK v1.5.1\pico-sdk')
PICO_SDK_PATH is C:/Program Files/Raspberry Pi/Pico SDK v1.5.1/pico-sdk
Defaulting PICO_PLATFORM to rp2040 since not specified.
Defaulting PICO platform compiler to pico_arm_gcc since not specified.
-- Defaulting build type to 'Release' since not specified.
PICO compiler is pico_arm_gcc
CMake Error at CMakeLists.txt:6 (project):
  Running

   'nmake' '-?'

  failed with:

   Das System kann die angegebene Datei nicht finden

-- Configuring incomplete, errors occurred!
See also "C:/Users/danie/Documents/Pico-v1.5.1/RP2040-Decoder/build/CMakeFiles/CMakeOutput.log".

Could it be the case that I have to install some Microsoft tool what is not mentioned?

gab-k, 2023-12-13:
Im not sure I personally don't have a windows machine at the moment so I can't try. Make sure you have Build tools for visual studio installed Section 9.2.2.3 of https://datasheets.raspberrypi.com/pico/getting-started-with-pico.pdf

If that does not work I would suggest following the steps described from section  9.2.2 onwards.

Space-Farmer, 2023-12-13:
Thanks for the help.
I thought that with the PICO SDK installer, all files and application for compilation etc. are installed.
Unfortunatly that was not the case....

Solution for me was to install the MS Build tools. (like described in the manuel from above, chapter 9.2.1)
After installation open the Developer command line for VS2022, then open the pico-env.cmd from RaspiPico SDK.
Then it compiles perfect.

Closed 2023-12-13.

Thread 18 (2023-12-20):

Function and light control

Space-Farmer, 2023-12-20:
Sorry to ask the next stupid question...
Great project that you shared!!
Setting into operation to drive forward and backward is already working nicely.
Today I started and want to controll the LEDs.
I tested the LEDs with grabbing the Voltage behind the rectivier (+V and GND), they are working fine.
Now I added each LED Row white/red color ; front/backside to one of the AUX pins.
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
I experimented with the CVs 257,261,265, 269 but it did not change anything.
I came to the point maybe I have to enable the PWM to the pins that they are modifyable.
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
For the PWM I used the values from wiki:
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
Which results to for GPIO 24,25,26,27
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
Additionaly I doublechecked the CV for Fx forward/reverse:
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
Please find also attached a readout of all CVs

[CVs.csv](https://github.com/gab-k/RP2040-Decoder/files/13733560/CVs.csv)

But unfortunatly the LEDs are still always on :-(
I hope you can support me with finding my mistake.

Thanks in advance.

gab-k, 2023-12-21:
Hi, I dont really clearly understand what you are trying to achieve? You are saying the LEDs are always on. When should the LEDs be off? Depending on direction?

Space-Farmer, 2023-12-24:
Hi, sorry, was a little late that day.

What I wanted to achieve was:
That the AUX0 is front light (forward direction) and only on when moving forward & Function0 enabled.
AUX1 is front light (reverse direction) and only on when moving reverse & Function0 enabled.
AUX2 is rear light (forward direction) and should only on when moving forward and pressing Function1 button.
AUX3 is rear light (reverse direction) and should only on when moving reverse and pressing Function1 button.

What happens: all lights are always on. No change with direction nor with enabling the Functions buttons inside visualization.

Did I miss something to enable for the application described above?
Is PWM and function control possible in parallel?
Did I need to consider the Signal negation by N-Mos of GPIO24-27?

Many thanks for your work on that project.
I wish you a merry Christmas and a happy new year.

Best Regards.

gab-k, 2023-12-26:
> Did I miss something to enable for the application described above?

Your CV's are mostly correct, bits 7 to 4 should not be set in CV257, CV261, CV265 and CV269.
So it should be CV257 = 1, CV261 = 2, CV265 = 4 and CV269 = 8 also I made a mistake in my description saying that the clock divider should be configured with a value of 10 to achieve 10kHz. In reality it needs to be set to a value of 9 in order to achieve a clock divider of 10 as a value of 0 corresponds to a divider of 1. However it should not cause the issue you have described as it only slightly alters the pwm frequency and has nothing to do with the issue you are describing.

> Is PWM and function control possible in parallel? Did I need to consider the Signal negation by N-Mos of GPIO24-27?

There isn't any negation to consider because when the gpio connected to the mosfet gate is set to 3.3V / "1" the mosfet will conduct and therefore connect the load to GND, closing the circuit and lighting the light. Regarding the first question, yes functions can be configured as PWM or regular output.

I tried to reproduce your issue but was not able to, you should draw a sketch of how you wired your lights (maybe on paper doesnt have to be anything special) to eliminate the possibility of wrong wiring. Also please try to set the CVs the way i mentioned above.

Space-Farmer, 2023-12-27:
>  bits 7 to 4 should not be set in CV257, CV261, CV265 and CV269
Reason why I marked the bit as "0" not as "1" was that all unused CVs where filled 255. And to distinguish between not configured and configured with "1" to "0" made more sense to me in that moment. Sorry that I did not had a deeper look to the code.

> So it should be CV257 = 1, CV261 = 2, CV265 = 4 and CV269 = 8
I made the changes also CV258,259,260,262,263,264,266,267,268,270,271,272 =0 to ensure that there is no interference. All LEDs are still always on. Maybe I missed some other CV, I will have a deeper look.
(when I change to program mode, LED are off, seems no short circuit)

> There isn't any negation to consider because when the gpio connected to the mosfet gate is set to 3.3V / "1" the mosfet will conduct and therefore connect the load to GND
That fits to my thoughts, thanks.

> draw a sketch of how you wired your lights
Let me try this in text form.
PCB V+ -> LED Anode
LED cathode -> resistor
resistor -> Pin header male
Pinheader female -> PCB AUX

SMD LEDs in parallel, 2 red 3 white. TOP-LED Case 3528, continues forward current: 50mA
red resistor 2kR, white resistor 500R

My next steps:
factory reset of the decoder
check with other decoder PCBs

gab-k, 2023-12-27:
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
It seems odd to me that your CVs are not the default value (see CV.h) normally the decoder should save the default values in  persistent flash memory after first flashing the software.

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

Bits 7 to 4 should not do anything anyway as the bits are always logical & masked with a bitmask containing the allowed pins only.

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
Looks good as far as I can tell.

> My next steps: factory reset of the decoder check with other decoder PCBs

Resetting would have been my next suggestion as well.

Space-Farmer, 2024-01-02:
I flashed the device with an spi programmer not with picoprobe.
Picoprobe is not running well on my side and with the spi programmer and a contact clamp it is very convinient to programm more parts in a row. (to get the bin files you have to uncomment one line inside cmake dile)

After resetting the default values where in Place.

And yes light and functions are working fine. Thanks for the Support.
Issue could be closed from my side. If you have further quesitions or you need readouts from the spi flashed parts feel free to ask.

Closed 2024-01-02.

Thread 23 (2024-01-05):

LDO problem

gab-k, 2024-01-05:
### Discussed in https://github.com/gab-k/RP2040-Decoder/discussions/17

<div type='discussions-op-text'>

<sup>Originally posted by **hebalazs** December 20, 2023</sup>
Hello, this is the first time I am using this project. I have some pieces of decoders. For programming, I use another open-source project (DCC-EX), and some of my decoders have died (RP2040 has a short circuit inside) due to the incorrect operation of the LDO. I measured the LDO voltage and observed a 7V peak during power-on. Currently, I have replaced the LDOs with [MCP1799T-3302H/TT](https://ww1.microchip.com/downloads/en/DeviceDoc/MCP1799-Data-Sheet-20006248A.pdf). It has the same package, and it has thermal and current protections. Now it seems the decoder is working properly. Have you experienced similar problems?
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
</div>

Please read the discussion above. I would not recommend using the PJ75AL33SA at the moment. Please choose an alternative SOT-23-3 3.3V LDO with similar specifications. Some regulators were already suggested by others and will probably work fine.

gab-k, 2024-01-27:
see https://github.com/gab-k/RP2040-Decoder/commit/bfa58bf5d6481cf426acf345e884aa84d8e5c236

Closed 2024-01-27.

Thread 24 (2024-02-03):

Marklin

alsig, 2024-02-03:
Hi,

I have just received a batch of decoders from JLCPCB. I'm able to communicate with the boards using the SWD interface and have successfully programmed the first.

I experiencing different issues. I have fried a couple of motor drivers.  I suspect that since I'm running Marklin the voltage levels are somewhat different than a DC/DCC system. The motor driver is rated for maximum of 26V but I can read 19V from my CS3. But that's properly an AC of some sort...

Another issue that I have is one board where the U1, the voltage regulator, get extremely hot after a few seconds. I'm able to connect to the mcu through SWD before I shut the power off... So something is working but other parts are drawing too much power...

So in short, have any one successfully tried these decoders on Marklin tracks?

Or do anybody have an idea to how I can modify the PCBs so they can work with Marklin?

/Jens

gab-k, 2024-02-09:
The issue regarding the motor driver seems odd, can't imagine that the CS3 puts out voltages > 26V. Regarding the voltage regulator, yes it is a bad design, it gets very hot especially at higher track voltages due to its linear regulation nature. An ugly but easy fix would be to just solder another regulator in something like a SOT-223 package (or similar) on the back side of the board.

probonopd, 2024-02-13:
Wouldn't some "rectified, step-down switch-mode converter with built-in internal power MOSFETs" ([example](https://www.monolithicpower.com/en/products/power-management/power-modules/mpm3612-33.html); I am not necessarily suggesting this particular model) be able to do the job more nicely than a linear (=inefficient and hot) converter?

gab-k, 2024-02-14:
In terms of efficiency its certainly the better option. However i decided against it due to higher cost and increased need for PCB space. Additionally the availability / potential replacements with the same pinout are better with an LDO. Replacing it with an SOT-89 part however might be a solution.

Closed 2024-05-05.

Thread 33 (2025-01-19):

Documentation quiestions

voroskoi, 2025-01-19:
Hi,

First of all, thank You for this work and sharing them online!

After reading the documentation I have a couple of quiestions. I was hoping You could answer them and I could make a PR with the clarifications for You in return.

1. "You can assemble the board yourself, but it’s best not to do so if you’re not familiar with soldering small components. Alternatively, you can order the board fully or partly assembled." - I have never ordered any PCB. I assume You talk about the possibility of ordering the SMD parts and soldering those together. On JLCPCB site there is an option for assembling the board, which everyone should take if they want to provide BOM and Pick and Place files and want a fully working board after the purchase, but They can also decide to order the board and solder everything at home. Is that right?
2. "Soldering the back of the PCB by hand is not too difficult." - On JLCPCB there is an option for "Assembly Side" with top, bottom and both sides. If I chose top side (which is the default) that means I have to make some soldering at home? Or You just happen to mention that the bottom half soldering is not that hard if somebody is already doing the top part?
3. I have not been able to figure out what to do with `netlist.ipc` and `designators.csv` while ordering the PCB. Do I need those?
4. On the [wiring](https://gab-k.github.io/RP2040-Decoder/sphinx/html/hardware/rev_1_0/hw_description.html#wiring-the-decoder) diagram: The `Load1` is using 3.3V to switch a LED or something like that. `Load0` on the other hand gets the DCC signal and voltage (up to 24V) directly when switched on, right? Can You name a use case for that?

Thank You!

gab-k, 2025-01-19:
> I have never ordered any PCB. I assume You talk about the possibility of ordering the SMD parts and soldering those together. On JLCPCB site there is an option for assembling the board, which everyone should take if they want to provide BOM and Pick and Place files and want a fully working board after the purchase, but They can also decide to order the board and solder everything at home. Is that right?

Yes, that is correct.

>  If I chose top side (which is the default) that means I have to make some soldering at home?

Yes, you would have to order the parts for the bottom side and assemble the bottom side by hand.

> Or You just happen to mention that the bottom half soldering is not that hard if somebody is already doing the top part?

Yes, that is basically what I meant, assembly of the top side and doing the bottom side yourself is a little bit more price effective. Assembling everything yourself is of course even cheaper.

>     3. I have not been able to figure out what to do with `netlist.ipc` and `designators.csv` while ordering the PCB. Do I need those?

No, you don't need those.

> On the [wiring](https://gab-k.github.io/RP2040-Decoder/sphinx/html/hardware/rev_1_0/hw_description.html#wiring-the-decoder) diagram: The `Load1` is using 3.3V to switch a LED or something like that. `Load0` on the other hand gets the DCC signal and voltage (up to 24V) directly when switched on, right?

Mostly correct, the load gets connected to VDC which is the rectified DCC voltage. The transistor then basically acts like a switch and switches the other side to GND potential.

> Can You name a use case for that?

You might have a classic 12V or 24V Halogen/Incandescent light for lighting.

voroskoi, 2025-01-21:
Thank You very much for those answers.

I have tried to use PCBWay as they have an order sharing system which makes ordering much easier for noobs like me, but they replied with a question I do not really understand:

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

Thank You!

voroskoi, 2025-01-22:
Nevermind, I have used KiCad for uploading the full project and they have accepted it.

Closed 2025-01-22.

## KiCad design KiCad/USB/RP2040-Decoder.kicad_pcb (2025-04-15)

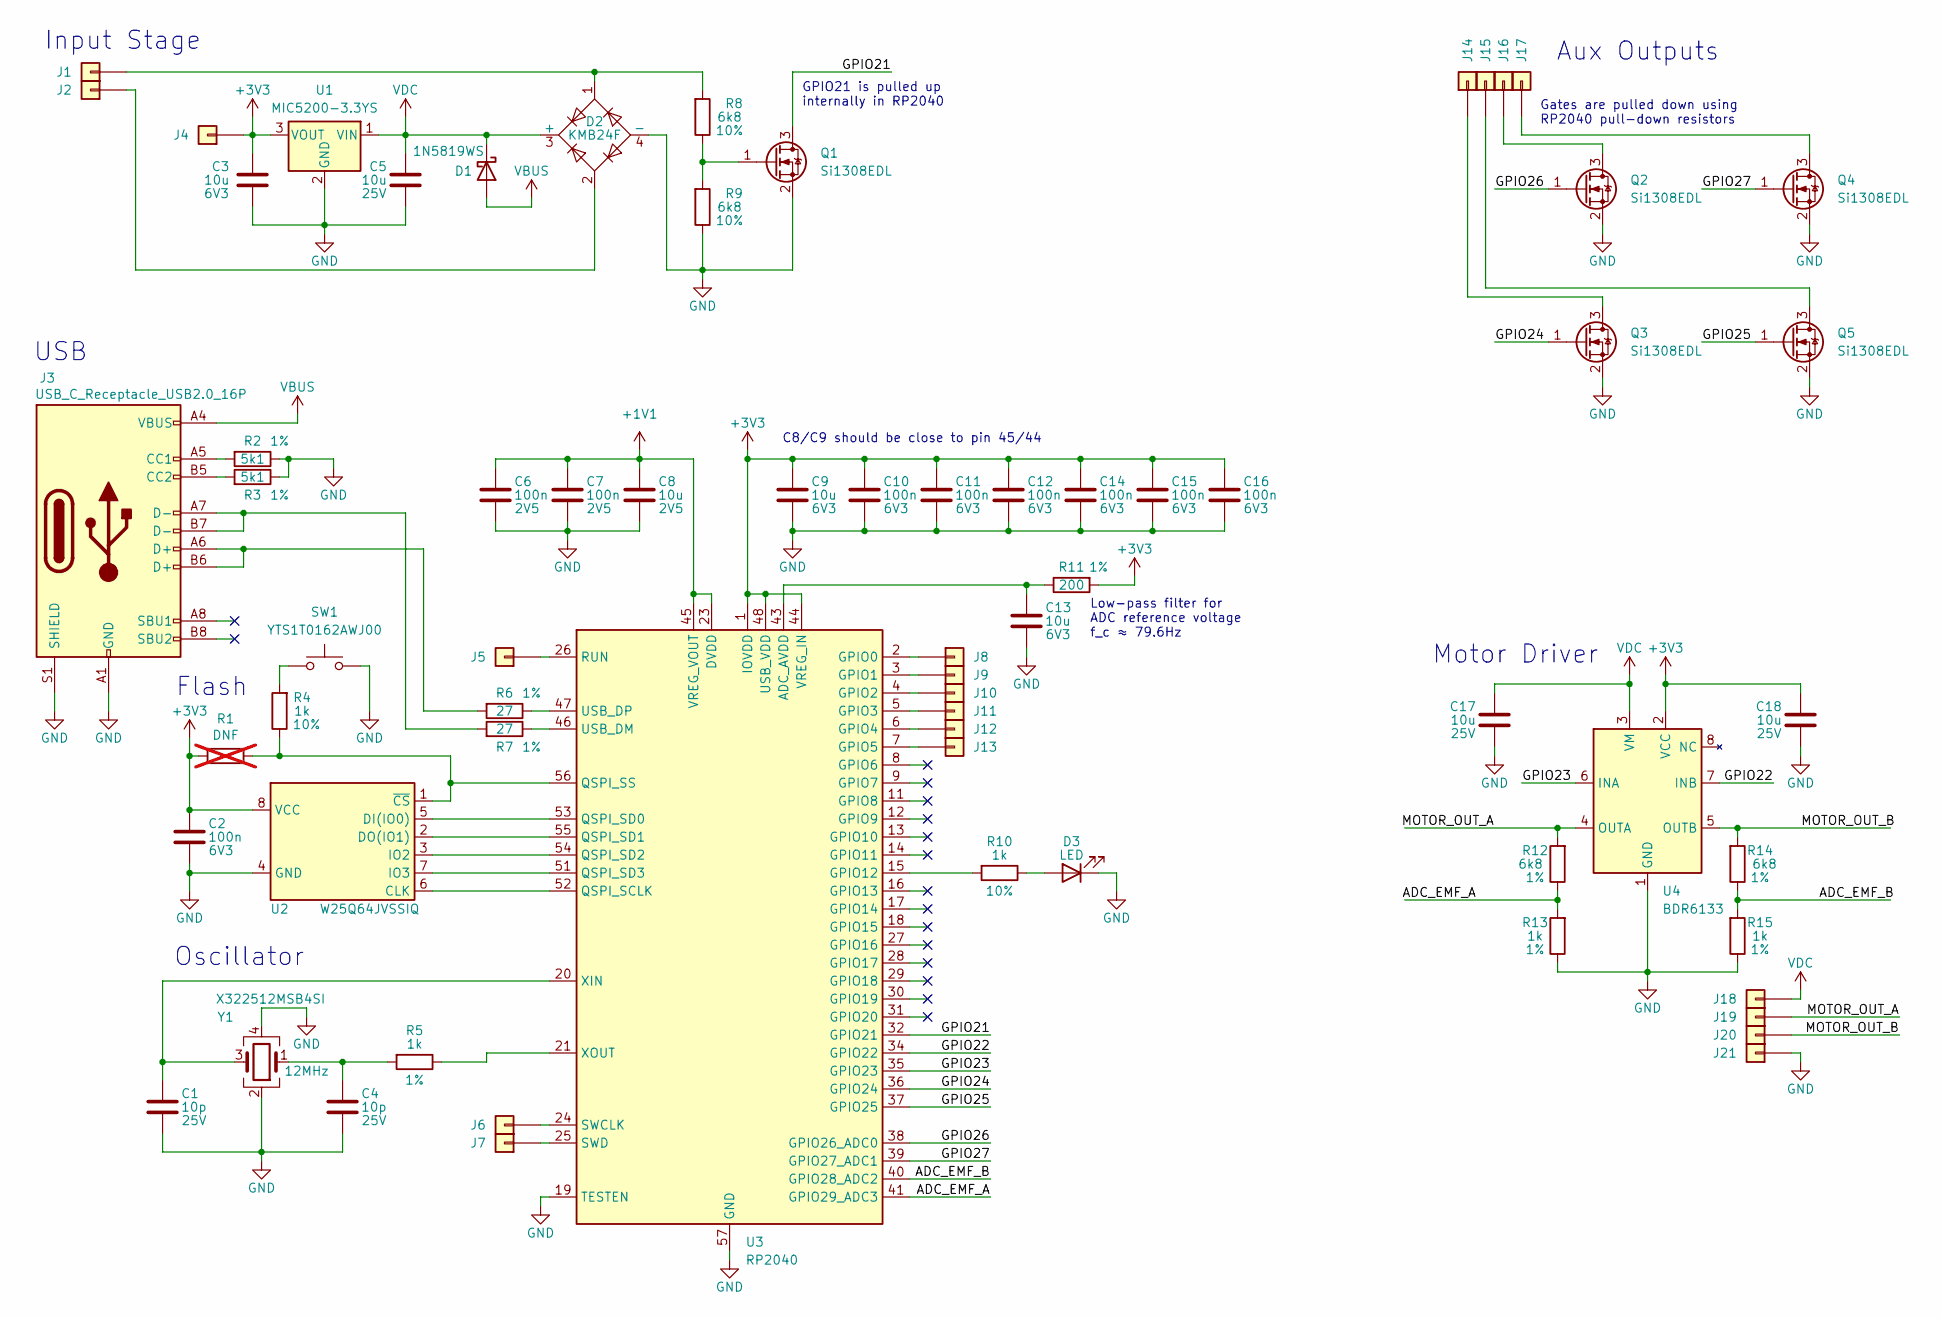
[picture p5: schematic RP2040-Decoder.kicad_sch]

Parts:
C1, C4: 10p; C_0402_1005Metric; Voltage 25V; LCSC Part # C32949
C2, C10, C11, C12, C14, C15, C16: 100n; C_0402_1005Metric; Voltage 6V3; LCSC Part # C1525
C3: 10u; C_0603_1608Metric; Voltage 6V3; LCSC Part # C96446
C5, C17, C18: 10u; C_0603_1608Metric; Voltage 25V; LCSC Part # C96446
C6, C7: 100n; C_0402_1005Metric; Voltage 2V5; LCSC Part # C1525
C8: 10u; C_0402_1005Metric; Voltage 2V5; LCSC Part # C15525
C9, C13: 10u; C_0402_1005Metric; Voltage 6V3; LCSC Part # C15525
D1: 1N5819WS; D_SOD-323_HandSoldering; LCSC Part # C191023
D2: KMB24F; TO-269AA; LCSC Part # C880910
D3: LED; LED_0603_1608Metric; LCSC Part # C2286
J1, J2, J4, J14, J15, J16, J17, J18, J21: Conn_01x01; TestPoint_Pad_D2.0mm
J3: USB_C_Receptacle_USB2.0_16P; USB_C_Receptacle_GCT_USB4105-xx-A_16P_TopMnt_Horizontal; LCSC Part # C2927038
J5, J6, J7, J8, J9, J10, J11, J12, J13: Conn_01x01; TestPoint_Pad_D1.5mm
J19, J20: Conn_01x01; TestPoint_Pad_1.5x1.5mm
Q1, Q2, Q3, Q4, Q5: Si1308EDL; SOT-323_SC-70; LCSC Part # C469327
R1: DNF; R_0402_1005Metric; not fitted
R2, R3: 5k1; R_0402_1005Metric; Tolerance 1%; LCSC Part # C25905
R4, R10: 1k; R_0402_1005Metric; Tolerance 10%; LCSC Part # C11702
R5, R13, R15: 1k; R_0402_1005Metric; Tolerance 1%; LCSC Part # C11702
R6, R7: 27; R_0402_1005Metric; Tolerance 1%; LCSC Part # C138021
R8, R9: 6k8; R_0402_1005Metric; Tolerance 10%; LCSC Part # C25917
R11: 200; R_0402_1005Metric; Tolerance 1%; LCSC Part # C25087
R12, R14: 6k8; R_0402_1005Metric; Tolerance 1%; LCSC Part # C25917
SW1: YTS1T0162AWJ00; SW_Push_1P1T_NO_Vertical_Wuerth_434133025816; LCSC Part # C3726363
U1: MIC5200-3.3YS; SOT-223; LCSC Part # C5343216
U2: W25Q64JVSSIQ; SOIC-8_5.23x5.23mm_P1.27mm; LCSC Part # C179171
U3: RP2040; QFN-56-1EP_7x7mm_P0.4mm_EP3.2x3.2mm; LCSC Part # C2040
U4: BDR6133; SOIC-8-1EP_3.9x4.9mm_P1.27mm_EP2.41x3.3mm_ThermalVias; LCSC Part # C2687793
Y1: X322512MSB4SI; Crystal_SMD_3225-4Pin_3.2x2.5mm; LCSC Part # C9002

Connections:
+1V1: C6.1, C7.1, C8.1, U3.23 (DVDD), U3.45 (VREG_VOUT), U3.50 (DVDD)
+3V3: C2.1, C3.1, C9.1, C10.1, C11.1, C12.1, C14.1, C15.1, C16.1, C18.1, J4.1, R1.2, R11.1, U1.3 (VOUT), U2.8 (VCC), U3.1 (IOVDD), U3.10 (IOVDD), U3.22 (IOVDD), U3.33 (IOVDD), U3.42 (IOVDD), U3.44 (VREG_IN), U3.48 (USB_VDD), U3.49 (IOVDD), U4.2 (VCC)
/ADC_EMF_A: R12.1, R13.2, U3.41 (GPIO29_ADC3)
/ADC_EMF_B: R14.1, R15.2, U3.40 (GPIO28_ADC2)
/GPIO21: Q1.3 (D), U3.32 (GPIO21)
/GPIO22: U3.34 (GPIO22), U4.7 (INB)
/GPIO23: U3.35 (GPIO23), U4.6 (INA)
/GPIO24: Q3.1 (G), U3.36 (GPIO24)
/GPIO25: Q5.1 (G), U3.37 (GPIO25)
/GPIO26: Q2.1 (G), U3.38 (GPIO26_ADC0)
/GPIO27: Q4.1 (G), U3.39 (GPIO27_ADC1)
/MOTOR_OUT_A: J19.1, R12.2, U4.4 (OUTA)
/MOTOR_OUT_B: J20.1, R14.2, U4.5 (OUTB)
GND: C1.2, C2.2, C3.2, C4.2, C5.2, C6.2, C7.2, C8.2, C9.2, C10.2, C11.2, C12.2, C13.2, C14.2, C15.2, C16.2, C17.2, C18.2, D2.4 (-), D3.1 (K), J3.A1 (GND), J3.A12 (GND), J3.B1 (GND), J3.B12 (GND), J3.S1 (SHIELD), J21.1, Q1.2 (S), Q2.2 (S), Q3.2 (S), Q4.2 (S), Q5.2 (S), R2.1, R3.1, R9.1, R13.1, R15.1, SW1.2, U1.2 (GND), U1.4 (GND), U2.4 (GND), U3.19 (TESTEN), U3.57 (GND), U4.1 (GND), U4.9 (GND), Y1.2, Y1.4
unnamed: C4.1, R5.2, Y1.1
unnamed: D3.2 (A), R10.1
unnamed: D2.1, J1.1, R8.2
unnamed: D2.2, J2.1
unnamed: J3.A5 (CC1), R2.2
unnamed: J3.B5 (CC2), R3.2
unnamed: J3.A6 (D+), J3.B6 (D+), R6.2
unnamed: J3.A7 (D-), J3.B7 (D-), R7.2
unnamed: J5.1, U3.26 (RUN)
unnamed: J6.1, U3.24 (SWCLK)
unnamed: J7.1, U3.25 (SWD)
unnamed: J8.1, U3.2 (GPIO0)
unnamed: J9.1, U3.3 (GPIO1)
unnamed: J10.1, U3.4 (GPIO2)
unnamed: J11.1, U3.5 (GPIO3)
unnamed: J12.1, U3.6 (GPIO4)
unnamed: J13.1, U3.7 (GPIO5)
unnamed: J14.1, Q3.3 (D)
unnamed: J15.1, Q5.3 (D)
unnamed: J16.1, Q2.3 (D)
unnamed: J17.1, Q4.3 (D)
unnamed: Q1.1 (G), R8.1, R9.2
unnamed: R4.2, SW1.1
unnamed: U2.6 (CLK), U3.52 (QSPI_SCLK)
unnamed: U2.5 (DI(IO0)), U3.53 (QSPI_SD0)
unnamed: U2.2 (DO(IO1)), U3.55 (QSPI_SD1)
unnamed: U2.3 (IO2), U3.54 (QSPI_SD2)
unnamed: U2.7 (IO3), U3.51 (QSPI_SD3)
unnamed: R1.1, R4.1, U2.1 (~CS), U3.56 (QSPI_SS)
unnamed: C13.1, R11.2, U3.43 (ADC_AVDD)
unnamed: R10.2, U3.15 (GPIO12)
unnamed: R7.1, U3.46 (USB_DM)
unnamed: R6.1, U3.47 (USB_DP)
unnamed: C1.1, U3.20 (XIN), Y1.3
unnamed: R5.1, U3.21 (XOUT)
VBUS: D1.2 (A), J3.A4 (VBUS), J3.A9 (VBUS), J3.B4 (VBUS), J3.B9 (VBUS)
VDC: C5.1, C17.1, D1.1 (K), D2.3 (+), J18.1, U1.1 (VIN), U4.3 (VM)

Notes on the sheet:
Gates are pulled down using RP2040 pull-down resistors
Motor Driver
GPIO21 is pulled up internally in RP2040
Aux Outputs
C8/C9 should be close to pin 45/44
USB
Oscillator
Low-pass filter for ADC reference voltage f_c  ≈ 79.6Hz
Flash
Input Stage

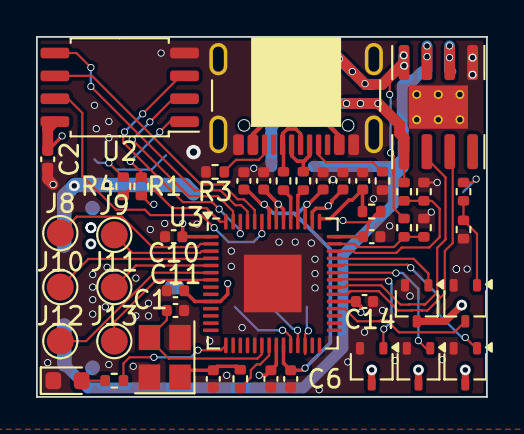
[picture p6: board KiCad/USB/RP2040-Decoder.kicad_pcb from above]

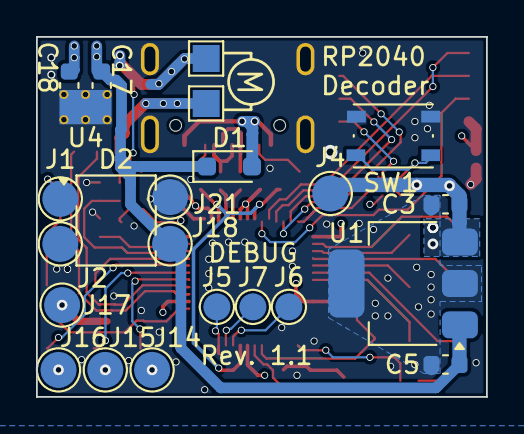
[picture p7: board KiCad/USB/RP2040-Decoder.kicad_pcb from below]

Board: 4 copper layers, 25.0 x 20.0 mm, 68 parts (22 on the bottom side), 51 nets.

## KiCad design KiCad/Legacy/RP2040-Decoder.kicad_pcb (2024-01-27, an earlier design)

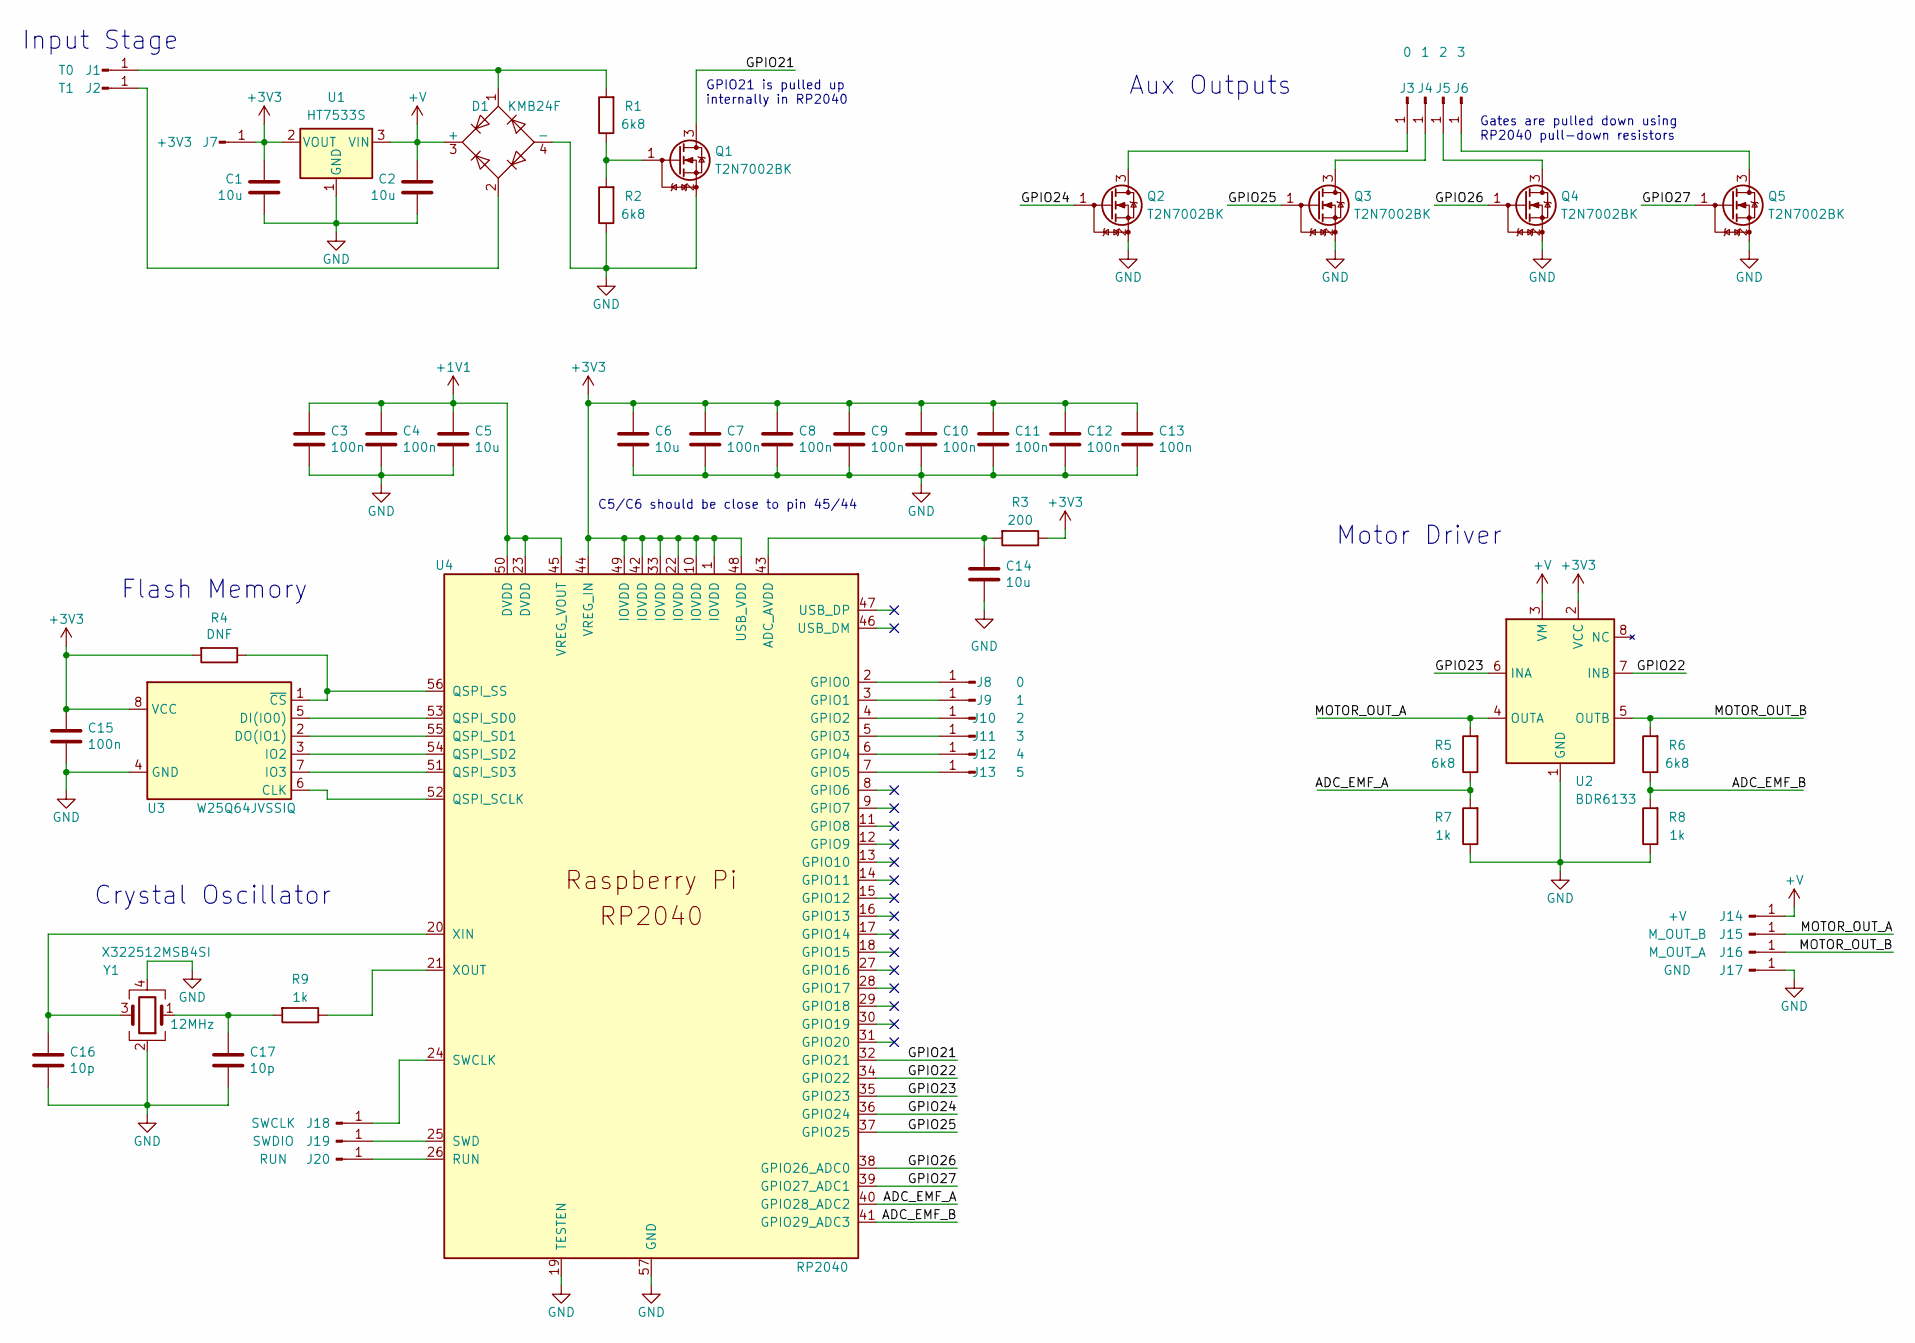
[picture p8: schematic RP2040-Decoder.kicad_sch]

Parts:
C1, C2, C5, C6, C14: 10u; C_0603_1608Metric
C3, C4, C7, C8, C9, C10, C11, C12, C13, C15: 100n; C_0603_1608Metric
C16, C17: 10p; C_0603_1608Metric
D1: KMB24F; TO-269AA
J1: T0; TestPoint_Pad_D2.0mm
J2: T1; TestPoint_Pad_D2.0mm
J3, J8: 0; TestPoint_Pad_D2.0mm
J4, J9: 1; TestPoint_Pad_D2.0mm
J5, J10: 2; TestPoint_Pad_D2.0mm
J6, J11: 3; TestPoint_Pad_D2.0mm
J7: +3V3; TestPoint_Pad_D2.0mm
J12: 4; TestPoint_Pad_D2.0mm
J13: 5; TestPoint_Pad_D2.0mm
J14: +V; TestPoint_Pad_D2.0mm
J15: M_OUT_B; TestPoint_Pad_D2.0mm
J16: M_OUT_A; TestPoint_Pad_D2.0mm
J17: GND; TestPoint_Pad_D2.0mm
J18: SWCLK; TestPoint_Pad_D2.0mm
J19: SWDIO; TestPoint_Pad_D2.0mm
J20: RUN; TestPoint_Pad_D2.0mm
Q1, Q2, Q3, Q4, Q5: T2N7002BK; SOT-23
R1, R2, R5, R6: 6k8; R_0603_1608Metric
R3: 200; R_0603_1608Metric
R4: DNF; R_0603_1608Metric
R7, R8, R9: 1k; R_0603_1608Metric
U1: HT7533S; SOT-23
U2: BDR6133; SOIC-8-1EP_3.9x4.9mm_P1.27mm_EP2.41x3.3mm_ThermalVias
U3: W25Q64JVSSIQ; SOIC-8_5.23x5.23mm_P1.27mm
U4: RP2040; QFN-56-1EP_7x7mm_P0.4mm_EP3.2x3.2mm
Y1: X322512MSB4SI; Crystal_SMD_3225-4Pin_3.2x2.5mm

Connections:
+1V1: C3.1, C4.1, C5.1, U4.23 (DVDD), U4.45 (VREG_VOUT), U4.50 (DVDD)
+3V3: C1.1, C6.1, C7.1, C8.1, C9.1, C10.1, C11.1, C12.1, C13.1, C15.1, J7.1, R3.1, R4.2, U1.2 (VOUT), U2.2 (VCC), U3.8 (VCC), U4.1 (IOVDD), U4.10 (IOVDD), U4.22 (IOVDD), U4.33 (IOVDD), U4.42 (IOVDD), U4.44 (VREG_IN), U4.48 (USB_VDD), U4.49 (IOVDD)
+V: C2.1, D1.3 (+), J14.1, U1.3 (VIN), U2.3 (VM)
/ADC_EMF_A: R5.1, R7.2, U4.40 (GPIO28_ADC2)
/ADC_EMF_B: R6.1, R8.2, U4.41 (GPIO29_ADC3)
/GPIO21: Q1.3 (D), U4.32 (GPIO21)
/GPIO22: U2.7 (INB), U4.34 (GPIO22)
/GPIO23: U2.6 (INA), U4.35 (GPIO23)
/GPIO24: Q2.1 (G), U4.36 (GPIO24)
/GPIO25: Q3.1 (G), U4.37 (GPIO25)
/GPIO26: Q4.1 (G), U4.38 (GPIO26_ADC0)
/GPIO27: Q5.1 (G), U4.39 (GPIO27_ADC1)
/MOTOR_OUT_A: J15.1, R5.2, U2.4 (OUTA)
/MOTOR_OUT_B: J16.1, R6.2, U2.5 (OUTB)
GND: C1.2, C2.2, C3.2, C4.2, C5.2, C6.2, C7.2, C8.2, C9.2, C10.2, C11.2, C12.2, C13.2, C14.2, C15.2, C16.2, C17.2, D1.4 (-), J17.1, Q1.2 (S), Q2.2 (S), Q3.2 (S), Q4.2 (S), Q5.2 (S), R2.1, R7.1, R8.1, U1.1 (GND), U2.1 (GND), U2.9 (GND), U3.4 (GND), U4.19 (TESTEN), U4.57 (GND), Y1.2, Y1.4
unnamed: C14.1, R3.2, U4.43 (ADC_AVDD)
unnamed: D1.1, J1.1, R1.2
unnamed: D1.2, J2.1
unnamed: J3.1, Q2.3 (D)
unnamed: J4.1, Q3.3 (D)
unnamed: J5.1, Q4.3 (D)
unnamed: J6.1, Q5.3 (D)
unnamed: J8.1, U4.2 (GPIO0)
unnamed: J9.1, U4.3 (GPIO1)
unnamed: J10.1, U4.4 (GPIO2)
unnamed: J11.1, U4.5 (GPIO3)
unnamed: J12.1, U4.6 (GPIO4)
unnamed: J13.1, U4.7 (GPIO5)
unnamed: J18.1, U4.24 (SWCLK)
unnamed: J19.1, U4.25 (SWD)
unnamed: J20.1, U4.26 (RUN)
unnamed: Q1.1 (G), R1.1, R2.2
unnamed: R4.1, U3.1 (~CS), U4.56 (QSPI_SS)
unnamed: C17.1, R9.2, Y1.1
unnamed: U3.2 (DO(IO1)), U4.55 (QSPI_SD1)
unnamed: U3.3 (IO2), U4.54 (QSPI_SD2)
unnamed: U3.5 (DI(IO0)), U4.53 (QSPI_SD0)
unnamed: U3.6 (CLK), U4.52 (QSPI_SCLK)
unnamed: U3.7 (IO3), U4.51 (QSPI_SD3)
unnamed: C16.1, U4.20 (XIN), Y1.3
unnamed: R9.1, U4.21 (XOUT)

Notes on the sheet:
Gates are pulled down using RP2040 pull-down resistors
Motor Driver
GPIO21 is pulled up internally in RP2040
Aux Outputs
Crystal Oscillator
C5/C6 should be close to pin 45/44
Flash Memory
Input Stage

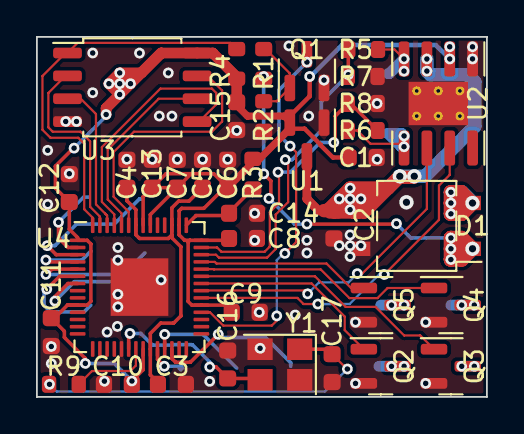
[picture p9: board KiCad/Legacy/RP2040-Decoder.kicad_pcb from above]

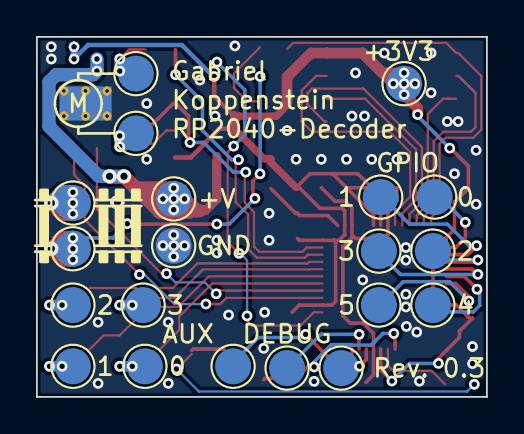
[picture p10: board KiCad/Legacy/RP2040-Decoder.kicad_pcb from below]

Board: 2 copper layers, 25.0 x 20.0 mm, 57 parts (20 on the bottom side), 41 nets.

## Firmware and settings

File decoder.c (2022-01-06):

//////////////////////////
//   RP2040-Decoder     //
// Gabriel Koppenstein  //
//////////////////////////

#include "CV.h"
#include "decoder.h"
#include <stdio.h>
#include "string.h"
#include "pico/stdlib.h"
#include "pico/multicore.h"
#include "hardware/pwm.h"
#include "hardware/adc.h"
#include "hardware/flash.h"
#include "hardware/irq.h"
#include "stdint.h"
const uint8_t *CV_ARRAY_FLASH = (const uint8_t *) (XIP_BASE + FLASH_TARGET_OFFSET);
bool active_functions[SIZE_ACTIVE_FUNCTIONS] = {false};
uint64_t last_bits = 0;
bool target_direction = true;
uint target_speed_step = 128;
uint current_target = 0;
bool reset_package_flag = false;
typedef struct pid_params{
    float k_p;
    float t_s;
    float a_1;
    float a_2;
    int sum_limit_max;
    int sum_limit_min;
    float output;
    int e;
    int e_prev;
    int e_sum;
}pid_params;
pid_params pid;
typedef struct measure_params{
    uint8_t delay_in_us;
    uint8_t total_iterations;
    uint8_t left_side_array_cutoff;
    uint8_t right_side_array_cutoff;
}measure_params;
measure_params msr;
struct repeating_timer pid_control_timer,speed_helper_timer;

int8_t check_for_package()  //returns number of bytes if valid bit-pattern is found. Otherwise -1 is returned.
{
    uint64_t package3Masked = last_bits & PACKAGE_MASK_3_BYTES;
    if (package3Masked == PACKAGE_3_BYTES) {
        return 3;
    }
    uint64_t package4Masked = last_bits & PACKAGE_MASK_4_BYTES;
    if (package4Masked == PACKAGE_4_BYTES) {
        return 4;
    }
    uint64_t package5Masked = last_bits & PACKAGE_MASK_5_BYTES;
    if (package5Masked == PACKAGE_5_BYTES) {
        return 5;
    }
    return -1;
}
void writeLastBit(bool bit) {
    last_bits <<= 1;
    last_bits |= bit;
}
int64_t readBit_alarm_callback(alarm_id_t id, void *user_data){
    writeLastBit(!gpio_get(DCC_INPUT_PIN));
    evaluation();
    return 0;
}

//start of transmission -> byte_n(address byte) -> ... -> byte_0(error detection byte) -> end of transmission
void bits_to_byte_array(int8_t number_of_bytes,uint8_t byte_array[]) {
    for (uint8_t i = 0; i < number_of_bytes; i++) {
        byte_array[i] = last_bits >> (i * 9 + 1);
    }
}

void adjust_pwm_level(uint16_t level)
{
    if(target_direction){
        pwm_set_gpio_level(MOTOR_PWM_REVERSE,0);
        pwm_set_gpio_level(MOTOR_PWM_FORWARD,level);
    }
    //Reverse
    else{
        pwm_set_gpio_level(MOTOR_PWM_FORWARD,0);
        pwm_set_gpio_level(MOTOR_PWM_REVERSE,level);
    }
}
void acknowledge(){
    target_direction = false;
    adjust_pwm_level(5000);
    busy_wait_ms(6);
    adjust_pwm_level(0);
}

void verify_cv_bit(uint16_t cv_address,bool bit_val, uint8_t bit_pos){
    uint8_t mask = 0b00000001;
    bool res = ( (CV_ARRAY_FLASH[cv_address] >> bit_pos) &mask ) == bit_val;
    if (res) {
        acknowledge();
    }
}
void verify_cv_byte(uint16_t cv_address, uint8_t cv_data){
    if (CV_ARRAY_FLASH[cv_address] == cv_data) acknowledge();
}
void write_cv_byte(uint16_t cv_address, uint8_t cv_data){
    //CV_7 read-only
    if (cv_address == 6){
    }
    else{
        //Reset all CVs to Default (CV_8; Value = 8)
        if (cv_address == 7 && cv_data == 8){
            flash_range_erase(FLASH_TARGET_OFFSET, FLASH_SECTOR_SIZE);
            flash_range_program(FLASH_TARGET_OFFSET, CV_ARRAY_DEFAULT, FLASH_PAGE_SIZE * 2);
            acknowledge();
        }
        else{
            uint8_t CV_ARRAY_TEMP[512] = {0};
            memcpy(CV_ARRAY_TEMP, CV_ARRAY_FLASH, sizeof(CV_ARRAY_TEMP));
            CV_ARRAY_TEMP[cv_address] = cv_data;
            flash_range_erase(FLASH_TARGET_OFFSET, FLASH_SECTOR_SIZE);
            flash_range_program(FLASH_TARGET_OFFSET, CV_ARRAY_TEMP, FLASH_PAGE_SIZE * 2);
            acknowledge();
        }
    }
}

bool reset_package_check(uint8_t number_of_bytes,const uint8_t byte_array[]){
    if (byte_array[number_of_bytes-1] == 0b00000000 && byte_array[number_of_bytes-2] == 0b00000000){
        target_speed_step = 1;
        //update_active_functions(0,0,37);
        return true;
    }else {
        return false;
    }
}

void program_mode(uint8_t number_of_bytes, const uint8_t byte_array[]){
    //Check for valid programming command ("address" 112-127)
    if (byte_array[number_of_bytes - 1]<128 && byte_array[number_of_bytes - 1]>111){
            uint8_t instruction_type_mask = 0b00001100;
            uint8_t instruction_type = instruction_type_mask & byte_array[number_of_bytes - 1];
            uint8_t cv_address_ms_bits_mask = 0b00000011;
            uint16_t cv_address_ms_bits = cv_address_ms_bits_mask & byte_array[number_of_bytes - 1];
            uint16_t cv_address = byte_array[number_of_bytes - 2] + (cv_address_ms_bits << 8);
            alarm_pool_destroy(pid_control_timer.pool);
            alarm_pool_destroy(speed_helper_timer.pool);
            multicore_reset_core1();
            uint32_t saved_interrupts = save_and_disable_interrupts();
            if (instruction_type == 0b000001000) {
                uint8_t bit_pos_mask = 0b00000111;
                uint8_t bit_pos = bit_pos_mask&byte_array[number_of_bytes - 3];
                uint8_t bit_val_mask = 0b00000001;
                uint8_t bit_val_uint = (byte_array[number_of_bytes - 3]>>3) & bit_val_mask;
                bool bit_val = bit_val_uint;
                verify_cv_bit(cv_address, bit_val, bit_pos);
            }
            else if (instruction_type == 0b000000100) {
                uint8_t cv_data = byte_array[number_of_bytes - 3];
                verify_cv_byte(cv_address, cv_data);
            }
            else if (instruction_type == 0b000001100) {
                uint8_t cv_data = byte_array[number_of_bytes - 3];
                write_cv_byte(cv_address, cv_data);
            }
            restore_interrupts(saved_interrupts);
            multicore_launch_core1(core1_entry);
    }
}

void set_outputs() {/*
    uint32_t GPIO_to_be_set = 0;
    //ensures that GPIO's that are used for inputs or PWM (motor) cannot be set HIGH
    uint32_t filter_forbidden_GPIO = 0b00000000000111111111111111111110;
    for (uint8_t i = 0; i < SIZE_ACTIVE_FUNCTIONS; i++) {
        if (active_functions[i]) {
            printf("F%u == 1\n",i);
            uint8_t func_cv_0 = CV_ARRAY_FLASH[260 + i * 8 - 4 * target_direction];
            uint8_t func_cv_1 = CV_ARRAY_FLASH[261 + i * 8 - 4 * target_direction];
            uint8_t func_cv_2 = CV_ARRAY_FLASH[262 + i * 8 - 4 * target_direction];
            uint8_t func_cv_3 = CV_ARRAY_FLASH[263 + i * 8 - 4 * target_direction];
            uint32_t func_cv = (func_cv_0) + (func_cv_1 << 8) + (func_cv_2 << 16) + (func_cv_3 << 24);
            GPIO_to_be_set = (GPIO_to_be_set | func_cv) & filter_forbidden_GPIO;
            uint32_t mask = 1;
            for (uint8_t j = 0; j < 32; j++)
            {
                uint32_t bit_value =  (GPIO_to_be_set&mask)>>j;
                //printf("GPIO: %u, set to: %d\n",j,bit_value);
                //gpio_put(j,bit_value);
                mask = mask<<1;
            }
            // printf("func_cv: %u\n",func_cv);
            // printf("func: F%u, direction: %u\n",func,direction);
            //printf("func_cv_0_index: %d  func_cv_1_index: %d  func_cv_2_index: %d  func_cv_3_index: %d  \n",4+257+i*8-4*direction,4+258+i*8-4*direction,4+259+i*8-4*direction,4+260+i*8-4*direction);
        }
    }*/
}

void update_active_functions(uint8_t function_number, uint8_t input_byte, uint8_t count) {
    uint8_t mask = 0b00000001;
    for (uint8_t i = 0; i < count; i++) {
        active_functions[i + function_number] = (input_byte & mask) == 0 ? 0 : 1;
        mask = mask << 1;
    }
}

bool error_detection(int8_t number_of_bytes, const uint8_t byte_array[]) {
    //Bitwise XOR for all Bytes -> Successful result is: "0000 0000"
    uint8_t xor_byte = 0;
    for (int i = 0; i < number_of_bytes; i++) {
        xor_byte = xor_byte ^ byte_array[i];
    }
    return (0 == xor_byte);
}

// Returns true for long address
bool is_long_address(uint8_t number_of_bytes, const uint8_t byte_array[]) {
    if ((byte_array[number_of_bytes - 1]>>6) == 0b00000011) return true;
    return false;
}

bool address_evaluation(uint8_t number_of_bytes,const uint8_t byte_array[]) {
    //Check for Idle Package
    if (byte_array[number_of_bytes - 1] == 255)
    {
        return false;
    }
    uint16_t read_address;
    //Long Address Package
    if (is_long_address(number_of_bytes, byte_array))
    {
        //start of transmission -> address_byte_1 -> address_byte_0 -> ... -> end of transmission
        uint16_t address_byte_1 = (byte_array[number_of_bytes - 1]) - 192;  //remove long address identifier bits
        uint16_t address_byte_0 = (byte_array[number_of_bytes - 2]);
        read_address = (address_byte_1 << 8) + address_byte_0;
        uint8_t long_address_mask = 0b00111111;
        uint16_t long_address = ((CV_ARRAY_FLASH[16]&long_address_mask)<<8)+CV_ARRAY_FLASH[17];
        return(long_address==read_address);
    }
    //Short Address Package
    else
    {
        //start of transmission ->  address_byte_0 -> ... -> end of transmission
        read_address = (byte_array[number_of_bytes - 1]);
        return (CV_ARRAY_FLASH[0] == read_address);
    }
}

void instruction_evaluation(uint8_t number_of_bytes,const uint8_t byte_array[]) {
    uint8_t command_byte_n;
    uint8_t command_byte_start_index;
    // start of transmission -> ... -> command_byte_n -> ... -> command_byte_0 -> ... -> end of transmission
    if (is_long_address(number_of_bytes,byte_array)) {
        command_byte_start_index = number_of_bytes - 3;
    } else {
        command_byte_start_index = number_of_bytes - 2;
    }
    command_byte_n = byte_array[command_byte_start_index];
    //0011-1111 (128 Speed Step Control) - 2 Byte length
    if (command_byte_n == 0b00111111){
        target_speed_step = byte_array[command_byte_start_index - 1];
        if(target_speed_step>127) target_direction = true;
        else target_direction = false;
    }
    // 10XX-XXXX (Function Group Instruction)
    if (command_byte_n >> 6 == 0b00000010){
        if (command_byte_n >> 5 == 0b00000100) // Functions F0-F4
        {
            update_active_functions(0, command_byte_n >> 4, 1); //F0
            update_active_functions(1, command_byte_n, 4);      //F1-F4
        } else {
            switch (command_byte_n >> 4) {
                // Functions F5-F8
                case 0b00001011:
                    update_active_functions(5, command_byte_n, 4);
                    break;
                // Functions F9-F12
                case 0b00001010:
                    update_active_functions(9, command_byte_n, 4);
                    break;
                default:
                    break;
            }
        }
    }
    //Feature Expansion Instruction 110X-XXXX
    if (command_byte_n >> 5 == 0b00000110)
    {
        switch (command_byte_n) {
            case 0b11011110: // F13-F20
                // printf("Functions F13-F20 Instruction\n");
                update_active_functions(13, byte_array[command_byte_start_index - 1], 8);
                break;
            case 0b11011111: // F21-F28
                // printf("Functions F21-F28 Instruction\n");
                update_active_functions(21, byte_array[command_byte_start_index - 1], 8);
                break;
            case 0b11011000: // F29-F36
                // printf("Functions F29-F36 Instruction\n");
                update_active_functions(29, byte_array[command_byte_start_index - 1], 8);
                break;
            default:
                break;
        }
    }
    //set_outputs();
}

//Interrupt handler for DCC Logic Signal
void gpio_callback_rise(unsigned int gpio, long unsigned int events) {
    add_alarm_in_us(87, &readBit_alarm_callback, NULL, true);
}

void evaluation(){
    int8_t number_of_bytes = check_for_package();
    if (number_of_bytes != -1) {
        uint8_t byte_array[SIZE_BYTE_ARRAY] = {0};
        bits_to_byte_array(number_of_bytes,byte_array);
        if(byte_array[number_of_bytes-3]==239 && byte_array[number_of_bytes-4]==151){
        }
        if (error_detection(number_of_bytes,byte_array)) {
            if (address_evaluation(number_of_bytes,byte_array)) {
                    reset_package_flag = false;
                    instruction_evaluation(number_of_bytes,byte_array);
                }
            else if (reset_package_flag){
                program_mode(number_of_bytes,byte_array);
            }
            else{
                reset_package_flag = reset_package_check(number_of_bytes,byte_array);
            }
        }
    }
}

void quicksort(uint16_t number[msr.total_iterations], int first, int last){
    int i, j, pivot, temp;
    if(first<last){
        pivot=first;
        i=first;
        j=last;
        while(i<j){
            while(number[i]<=number[pivot]&&i<last)
                i++;
            while(number[j]>number[pivot])
                j--;
            if(i<j){
                temp=number[i];
                number[i]=number[j];
                number[j]=temp;
            }
        }
        temp=number[pivot];
        number[pivot]=number[j];
        number[j]=temp;
        quicksort(number,first,j-1);
        quicksort(number,j+1,last);
    }
}

uint calc_end_target(){
    //Forward
    if(target_direction){
        if (target_speed_step == 128) return 0;
        else return (target_speed_step - 129) * CV_ARRAY_FLASH[59];
    }
    //Reverse
    else {
        if (target_speed_step == 0) return 0;
        else return (target_speed_step-1) * CV_ARRAY_FLASH[59];
    }
}

bool speed_helper() {
    uint8_t accel_rate = CV_ARRAY_FLASH[2];
    uint8_t decel_rate = CV_ARRAY_FLASH[3];
    uint end_target = calc_end_target();
    static uint8_t speed_helper_counter;
    //Emergency Stop
    if (target_speed_step == 129 || target_speed_step==1) {
        current_target = 0;
        speed_helper_counter = 0;
    }
    //Acceleration
    else if (end_target > current_target && speed_helper_counter == accel_rate) {
        current_target += CV_ARRAY_FLASH[59];
        speed_helper_counter = 0;
    }
    //Deceleration
    else if (end_target < current_target && speed_helper_counter == decel_rate) {
        current_target -= CV_ARRAY_FLASH[59];
        speed_helper_counter = 0;
    }
    else{
        speed_helper_counter++;
    }
    return true;
}

int measure(){
    pwm_set_gpio_level(MOTOR_PWM_FORWARD,0);
    pwm_set_gpio_level(MOTOR_PWM_REVERSE,0);
    adc_select_input(!target_direction);
    busy_wait_us(msr.delay_in_us);
    int sum = 0;
    // ≈ 270us
    uint16_t adc_values[msr.total_iterations];
    for (int i = 0; i < msr.total_iterations; ++i) {
        adc_values[i] = adc_read();
    }
    // Worst Case ≈ 415us
    quicksort(adc_values, 0, msr.total_iterations - 1);
    for (uint8_t i = msr.left_side_array_cutoff; i < msr.total_iterations - msr.right_side_array_cutoff ; ++i) {
        sum = sum+adc_values[i];
    }
    return sum/(msr.total_iterations - 20);
}

bool pid_control(struct repeating_timer *t){
    pid.e = (int)current_target - measure();
    pid.e_sum = pid.e_sum + pid.e;
    if (pid.e_sum > pid.sum_limit_max) pid.e_sum = pid.sum_limit_max;
    else if (pid.e_sum < pid.sum_limit_min) pid.e_sum = pid.sum_limit_min;
    pid.output +=   (pid.k_p * (float)pid.e) +
                    (pid.a_1 * (float)pid.e_sum) +                         //  k_i*t_s*e_sum
                    (pid.a_2 * (float)(pid.e - pid.e_prev));                //  (k_d/t_s)*(e-e_prev)
    pid.e_prev = pid.e;
    if (current_target == 0) pid.output = 0;
    else if (pid.output > 5000) pid.output = 5000;
    else if (pid.output < 1000) pid.output = 1000;
    adjust_pwm_level((uint16_t )pid.output);
    return true;
}

void init_pid(){
    pid.k_p = ((float)CV_ARRAY_FLASH[48] / 1024);
    pid.t_s = ((float)CV_ARRAY_FLASH[47] / 1000);
    pid.a_1 = ((float)CV_ARRAY_FLASH[49] / 256) * pid.t_s ;         //  k_i*t_s
    pid.a_2 = ((float)CV_ARRAY_FLASH[50] / 16384) / pid.t_s;        //  k_d/t_s                                                                     //  k_d/t_s
    pid.sum_limit_max = CV_ARRAY_FLASH[51] * 10;
    pid.sum_limit_min = CV_ARRAY_FLASH[52] * (-10);
    msr.total_iterations = CV_ARRAY_FLASH[60];
    msr.delay_in_us = CV_ARRAY_FLASH[61];
    msr.left_side_array_cutoff = CV_ARRAY_FLASH[62];
    msr.right_side_array_cutoff = CV_ARRAY_FLASH[63];
}

void init_pwm(uint gpio) {
    uint slice_num = pwm_gpio_to_slice_num(gpio);
    uint32_t wrap_counter = 5000;                  // 5000 Cycles @ 125MHz for 1 Period -> 25kHz
    pwm_set_wrap(slice_num, wrap_counter);
    pwm_set_gpio_level(gpio,0);
    pwm_set_clkdiv(slice_num,1);
    pwm_set_enabled(slice_num, true);
}

void print_cv_array(const uint8_t *buf, size_t len) {
    for (size_t i = 0; i < len; ++i) {
        printf("CV_%u: %02x",i+1, buf[i]);
        if (i % 4 == 3)
            printf("\n");
        else
            printf(" ");
    }
}

void core1_entry() {
    if(gpio_get_function(MOTOR_PWM_FORWARD)!=4){
        gpio_set_function(MOTOR_PWM_FORWARD, GPIO_FUNC_PWM);
        gpio_set_function(MOTOR_PWM_REVERSE, GPIO_FUNC_PWM);
        adc_init();
        adc_gpio_init(V_EMF_ADC_PIN_FORWARD);
        adc_gpio_init(V_EMF_ADC_PIN_REVERSE);
        init_pwm(MOTOR_PWM_FORWARD);
        init_pwm(MOTOR_PWM_REVERSE);
        init_pid();
    }
    alarm_pool_add_repeating_timer_ms(alarm_pool_create(0,1),
                                      //-CV_ARRAY_FLASH[47],
                                      5,
                                      pid_control,
                                      NULL,
                                      &pid_control_timer);
    irq_set_priority(0,0x00); // 0x00 is equivalent to the highest priority!
    alarm_pool_add_repeating_timer_ms(alarm_pool_create(1,1),
                                      7,
                                      speed_helper,
                                      NULL,
                                      &speed_helper_timer);
    while (1);
}

int main() {
    busy_wait_ms(1000);
    stdio_init_all();
    gpio_init(DCC_INPUT_PIN);
    gpio_set_dir(DCC_INPUT_PIN, GPIO_IN);
    multicore_launch_core1(core1_entry);
    gpio_set_irq_enabled_with_callback(DCC_INPUT_PIN, GPIO_IRQ_EDGE_RISE, true, &gpio_callback_rise);
    printf("Launched successfully.\n");
    while (1);
}

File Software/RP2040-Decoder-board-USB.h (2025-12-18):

/*
 * Copyright (c) 2020 Raspberry Pi (Trading) Ltd.
 *
 * SPDX-License-Identifier: BSD-3-Clause
 */

// -----------------------------------------------------
// NOTE: THIS HEADER IS ALSO INCLUDED BY ASSEMBLER SO
//       SHOULD ONLY CONSIST OF PREPROCESSOR DIRECTIVES
// -----------------------------------------------------

// Modified version of "boards/pico.h" for using the RP2040-Decoder board

// pico_cmake_set PICO_PLATFORM=rp2040

#ifndef _BOARDS_RP2040_DECODER_H
#define _BOARDS_RP2040_DECODER_H

// For board detection
#define RP2040_DECODER

// Decoder ID (CV_109)
#define DECODER_ID 2

// In case the xosc takes longer to stabilize than usual
#ifndef PICO_XOSC_STARTUP_DELAY_MULTIPLIER
#define PICO_XOSC_STARTUP_DELAY_MULTIPLIER 64
#endif

// --- UART ---
#ifndef PICO_DEFAULT_UART
#define PICO_DEFAULT_UART 0
#endif
#ifndef PICO_DEFAULT_UART_TX_PIN
#define PICO_DEFAULT_UART_TX_PIN 0
#endif
#ifndef PICO_DEFAULT_UART_RX_PIN
#define PICO_DEFAULT_UART_RX_PIN 1
#endif

// --- LED ---
#ifndef RP2040_DECODER_DEFAULT_LED_PIN
#define RP2040_DECODER_DEFAULT_LED_PIN 12
#endif

// --- FLASH ---

// Flash size is 8 MiB for W25Q64JVSSIQ if you decide to use another capacity flash IC change the size to the corresponding value
// 8MiB = (8 * 1024 * 1024) bytes = 8388608 bytes
#ifndef PICO_FLASH_SIZE_BYTES
#define PICO_FLASH_SIZE_BYTES 8388608
#endif

// Offset from base address used for saving CV_ARRAY_FLASH - in this case one sector size from the end of flash
#define FLASH_TARGET_OFFSET (PICO_FLASH_SIZE_BYTES-FLASH_SECTOR_SIZE)

// For some reason the clock divider of 4 is necessary, otherwise the controller occasionally hard faults
// Another workaround could be to run code from RAM but this seems to work fine
#ifndef PICO_FLASH_SPI_CLKDIV
#define PICO_FLASH_SPI_CLKDIV 4
#endif


#ifndef PICO_RP2040_B0_SUPPORTED
#define PICO_RP2040_B0_SUPPORTED 1
#endif

// Other pins
// GPIO used for DCC-Signal, Motor PWM or ADC
#define DCC_INPUT_PIN 21u
#define MOTOR_FWD_PIN 23u
#define MOTOR_REV_PIN 22u
#define FWD_V_EMF_ADC_PIN 29u
#define REV_V_EMF_ADC_PIN 28u
#define FWD_V_EMF_ADC_CHANNEL (FWD_V_EMF_ADC_PIN-26u)
#define REV_V_EMF_ADC_CHANNEL (REV_V_EMF_ADC_PIN-26u)


#if LOGLEVEL != 0
   // GPIO used directly (GPIO 2-5 incl.) as outputs or to switch auxiliary output transistors (GPIO 24-27 incl.)
   #define GPIO_OUTPUT_PIN_MASK ((1u<<24) | (1u<<25) | (1u<<26) | (1u<<27) | (1u<<5) | (1u<<4) | (1u<<3) | (1u<<2))
#else
   // GPIO used directly (GPIO 0-5 incl.) as outputs or to switch auxiliary output transistors (GPIO 24-27 incl.)
   #define GPIO_OUTPUT_PIN_MASK ((1u<<24) | (1u<<25) | (1u<<26) | (1u<<27) | (1u<<5) | (1u<<4) | (1u<<3) | (1u<<2) | (1u<<1) | (1u<<0))
#endif

// GPIO pin mask to prevent setting illegal GPIOs (ADC, Motor, DCC Input Pin)
// When logging to stdio using UART is enabled do NOT use PICO_DEFAULT_UART_TX_PIN and PICO_DEFAULT_UART_RX_PIN as GPIO/PWM outputs
#if (LOGLEVEL != 0) && (STDIO_UART_ENABLED != 0)
    #define GPIO_ILLEGAL_MASK ((1u<<DCC_INPUT_PIN) | (1u<<MOTOR_FWD_PIN) | (1u<<MOTOR_REV_PIN) | (1u<<FWD_V_EMF_ADC_PIN) | (1u<<REV_V_EMF_ADC_PIN) | (1u<<PICO_DEFAULT_UART_TX_PIN) | (1u<<PICO_DEFAULT_UART_RX_PIN))
#else
    #define GPIO_ILLEGAL_MASK ((1u<<DCC_INPUT_PIN) | (1u<<MOTOR_FWD_PIN) | (1u<<MOTOR_REV_PIN) | (1u<<FWD_V_EMF_ADC_PIN) | (1u<<REV_V_EMF_ADC_PIN))
#endif

// GPIO pin mask with allowed outputs (AUX & GPIO (configured as outputs))
#define GPIO_ALLOWED_OUTPUTS (GPIO_OUTPUT_PIN_MASK) & ~(GPIO_ILLEGAL_MASK)


#endif

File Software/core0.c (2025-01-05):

//////////////////////////
//   RP2040-Decoder     //
// Gabriel Koppenstein  //
//      core0.c         //
//////////////////////////

#include "core0.h"

// Define pointer to CV array stored in flash memory, FLASH_TARGET_OFFSET is defined in CMakeLists.txt and depending on flash size,
// it gets stored in the highest address flash sector possible, to avoid interference with the program code.
// CMakelists.txt also checks for program code exceeding past the last sector. Just have to make sure the correct flash size is set in CMakeLists.txt
const uint8_t *CV_ARRAY_FLASH = (const uint8_t *) (XIP_BASE + FLASH_TARGET_OFFSET);

// level_table is used to store pwm levels for any output using PWM
uint16_t level_table[sizeof(uint32_t)*8] = {0};

// Volatile due to modification in gpio interrupt context 
volatile absolute_time_t falling_edge_time, rising_edge_time;

// Input bit buffer for DCC signal
uint64_t input_bit_buffer = 0;
dcc_ring_buffer_t dcc_r_buf = {0};


static void increment_ring_buffer_idx(size_t * idx, uint8_t ring_buffer_length) {
    // Takes index variable as a pointer and increments it by 1. When index reaches the end of the ring buffer, it wraps around.
    // The wrap around value is the length of the ring buffer.
    *idx = (*idx + 1) % ring_buffer_length;
}

static size_t get_flash_size() {
    // Function to read the flash size of the chip, used for debugging/testing purposes
    // Prepare TX and RX buffers for reading the JEDEC ID
    uint8_t tx_buf[4] = { FLASH_CMD_READ_JEDEC_ID, 0, 0, 0 }; // Send the 0x9F command
    uint8_t rx_buf[4] = { 0, 0, 0, 0 }; // RX buffer for the response
    size_t buf_size = sizeof(tx_buf);
    void * params[] = {tx_buf, rx_buf, &buf_size};
    int ret_val = flash_safe_execute(call_flash_do_cmd, params, FLASH_TIMEOUT_IN_MS);
    if (ret_val != PICO_OK){
        set_error(FLASH_SIZE_READBACK_FAILURE);
        return 0;
    }

    // The third byte of the response (rxbuf[3]) contains the log2 size (e.g., 0x18 for 16 MB)
    if (rx_buf[3] == 0) {
        set_error(FLASH_SIZE_READBACK_FAILURE);
        return 0;
    }

    // Calculate the actual size (2^size_code bytes)
    size_t flash_size = (1u<<rx_buf[3]);
    
    // Return the flash size in bytes
    return flash_size;
}

void hardfault_handler(void) {
    // Custom HardFault handler
    // Log hardfault
    LOG(1, "HARDFAULT @ core%u!\n", get_core_num());
    LOG(1, "Rebooting...\n")

    // Hardfault can't be recovered, trigger the watchdog to reset the system
    watchdog_reboot(0, 0, 1);
}

static void trigger_hardfault(void) {
    // Force a hardfault, used for debugging/testing purposes
    __asm volatile("UDF #0"); // Undefined instruction
}

static void call_flash_range_erase(void *param) {
    // This function will be called when it's safe to call flash_range_erase
    // Always erases one sector, see FLASH_SECTOR_SIZE
    // Flash can only be erased in sectors, which effectively sets all bits to 1
    // Flash can than be programmed by setting bits to 0
    // Extract the parameters
    uint32_t offset = ((uintptr_t*)param)[0];
    uint32_t byte_count = ((uintptr_t*)param)[1];
    // Check for offset alignment (Must be aligned to a 4096-byte flash sector) 
    // Check byte count (Must be a multiple of 4096 bytes (one sector))
    if ((offset % FLASH_SECTOR_SIZE != 0) || (byte_count % FLASH_SECTOR_SIZE !=0)) {
        set_error(FLASH_SAFE_EXECUTE_PROGRAM_FAILURE);
        return;
    }
    flash_range_erase(offset, byte_count);
}

static void call_flash_range_program(void *param) {
    // This function will be called when it's safe to call flash_range_program
    // Extract the parameters
    uint32_t offset = ((uintptr_t*)param)[0];
    uint32_t byte_count = ((uintptr_t*)param)[1];
    const uint8_t *data = (const uint8_t *)((uintptr_t*)param)[2];
    // Check for offset alignment (Must be aligned to a 256-byte flash page)
    // Check byte count (Must be a multiple of 256 bytes (one page))
    if ((offset % FLASH_PAGE_SIZE != 0) || (byte_count % FLASH_PAGE_SIZE != 0)) {
        set_error(FLASH_SAFE_EXECUTE_PROGRAM_FAILURE);
        return;
    }
    flash_range_program(offset, data, byte_count);
}

static void call_flash_do_cmd(void *param) {
    // This function will be called when it's safe to call flash_do_cmd
    // Cast void pointer to void pointer array
    void **params = (void **)param;
    // Extract the parameters
    uint8_t * tx_buf = (uint8_t *)params[0];
    uint8_t * rx_buf = (uint8_t *)params[1];
    uint8_t * size_ptr = (uint8_t *)params[2];
    flash_do_cmd(tx_buf, rx_buf, *size_ptr);
}

unsigned int absolute_val(int x) {
    // Extract the sign bit
    int mask = x >> (sizeof(x) * 8 - 1); 
    return (x + mask) ^ mask;
}

static uint16_t two_std_dev(const uint16_t arr[], const uint32_t length) {
    // Calculate arithmetic average
    uint64_t sum = 0;
    for (uint32_t i = 0; i < length; ++i) {
        sum += arr[i];
    }
    const uint64_t x_avg = sum / length;

    // Calculate sample variance and sampled standard deviation
    sum = 0;
    for (uint32_t i = 0; i < length; ++i) {
        sum += (arr[i] - x_avg) * (arr[i] - x_avg);
    }
    const uint16_t variance = sum / (length-1);
    const uint16_t std_dev = (uint16_t) sqrtf((float) variance);

    // Sum every element that is within two times the sampled standard deviation and compute new average
    sum = 0;
    uint32_t counter = 0;
    for (uint32_t i = 0; i < length; ++i) {
        const uint32_t diff = absolute_val(arr[i] - x_avg);
        if ( diff <= 2*std_dev ){
            sum += arr[i];
            counter++;
        }
    }
    return sum / counter;
}
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

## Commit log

2021-08-25 error detection + address & command evaluation
    [multicore.c]
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2021-09-03 PWM-Period adjustable, Vmin Vmax implemented, fixed alarm_callback, fixed FIFO IRQ
    [multicore.c]
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2021-09-27 Implemented Basic Programming features, changed speed control (speed_helper function with timed interrupt)
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2022-01-03 fixed acknowledge bit/byte read routine, many small fixes and improvements
    [multicore.c]
2022-01-04 mainly changes in ACK, CV read/write, they should be reliable now (Core1 shutdown during read & write Acknowledge due to conflict of PWM functions)
2022-01-06 - renamed multicore.c to decoder.c and header files respectively - several changes to pid_control and speed_helper - measurements are now being "filtered" (x smallest and y biggest values will be dis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
2022-01-27 - Correction for Zener Diode Voltage - Changes to Header Files
    [core0.c, core1.c]
2022-01-29 git commit -a
    [RP2040-Decoder-Rev_0_2.kicad_sch]
2022-01-30 PCB and Schematic
    [RP2040-Decoder-Rev_0_2.kicad_pcb, RP2040-Decoder-Rev_0_2.kicad_sch]
2022-01-31 PCB & svg
    [RP2040-Decoder-Rev_0_2.kicad_sch]
2022-01-31 -changes to gitignore regarding KiCad files -changes to svg Files & Schematic ( Missing Net (GPIO) @ Input Stage)
    [RP2040-Decoder-Rev_0_2.kicad_pcb, RP2040-Decoder-Rev_0_2.kicad_sch]
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2022-02-01 Slight changes to schematic & progress on PCB design
    [RP2040-Decoder-Rev_0_2.kicad_pcb, RP2040-Decoder-Rev_0_2.kicad_sch]
2022-02-07 removed 47k resistor
    [RP2040-Decoder-Rev_0_2.kicad_sch]
2022-02-16 - Changes to sorting in measure() function - Changes to Zener Voltage Correction / measure now returns value in volts - Changes to Motor control - Resistor values changed - Created BOM
    [RP2040-Decoder-Rev_0_2.csv, RP2040-Decoder-Rev_0_2.kicad_sch]
2022-02-20 added startup offset to establish a baseline duty cycle at which the motor starts to spin
2022-02-23 - implemented linear approximation for pwm duty cycle offset (feed forward) - changed pid params and variables in measure() from float to integers - implemented Motor PWM Frequency CV - improved ackn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
    [core0.c, core1.c]
2022-02-28 Finished Board
    [RP2040-Decoder-Rev_0_2.csv, RP2040-Decoder-Rev_0_2.kicad_pcb, RP2040-Decoder-Rev_0_2.kicad_sch]
2022-03-01 small changes to B.Silkscreen and B.Fab
    [RP2040-Decoder-Rev_0_2.kicad_pcb]
2022-03-01 small changes to schematic and update to docs/svg
    [RP2040-Decoder-Rev_0_2.kicad_sch]
2022-03-02 -updated docs/png -slight change to f.silkscreen
    [RP2040-Decoder-Rev_0_2.kicad_pcb]
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2022-03-05 - improved PIN_MASK definitions; -implemented adc offset adjustment; - implemented startup checks for: factory flash setting, adc offset adjustment, motor offset adjustment; - implemented adc_offset 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
    [core0.c]
2022-03-06 - changes to ADC offset adjustment; - changes to output set function; - cv_setup_check() now waits for core1 to launch also after programming
2022-03-12 - remove m_pwm_offset_adjustment; - offset now adjusted in pid_control loop; - pid sampling time depends on speed step; - speed table implemented & and init function;
2022-05-02 AUX GPIO are now 24-27, ADC GPIO are now 28 and 29 DCC_IN is now 21 - Board Revision is now "0.3" - Omitted Rev. in Kicad filenames
    [RP2040-Decoder.kicad_pcb, RP2040-Decoder.kicad_sch]
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2022-07-28 - Reduced amount of global variables. Many variables are now initialized in main() and core1_entry() respectively and then passed as pointer. - Updates in speed steps are passed via multicore fifo. -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
2022-08-01 - added shared.c file containing functions that can be accessed from both cores - revised CV programming especially writing - Core 1 is only started when valid package with correct address is receive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
    [core0.c, core1.c]
2022-08-02 - Added long address svg - Direction is now preserved on packet timeout - Address > 127 can no longer be written to flash as it is not valid
    [core0.c, core1.c]
2022-08-03 - Minor changes to variable names, comments & formatting - Removed obsolete parameter previously used in program_mode - Added correction constant regarding base pwm measurement - Revised GPIO definit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
    [core0.c, core1.c]
2022-08-06 - added files for documentation - fixed undesired behaviour for direction change while decelerating - adjusted default value for CV_54 & CV_55
    [core0.c, core1.c]
2023-01-09 fix writing CV_1 - the default case was missing
    [core0.c]
2023-05-08 more debug printfs, disabled function usage of gpio0/1, disabled usb interface to save some 25kb in the firmware image
2023-10-15 fixed wrong parameter in measure() function call
    [core1.c]
2023-12-04 created USB and non-USB folders; added USB schematic
    [RP2040-Decoder.kicad_pcb, RP2040-Decoder.kicad_sch, USB4105-GF-A.stp]
2023-12-04 Changes to schematic, Created PCB
    [RP2040-Decoder.kicad_pcb, RP2040-Decoder.kicad_sch]
2023-12-05 added pcb constraints, changed designators, updated footprints and 3d-models, created board outline
    [RP2040-Decoder.kicad_pcb, RP2040-Decoder.kicad_sch]
2023-12-14 USB PCB routing, minor changes to schematic
    [RP2040-Decoder.kicad_pcb, RP2040-Decoder.kicad_sch]
2023-12-20 PCB Routing
    [RP2040-Decoder.kicad_pcb]
2023-12-26 Fix missing Bitmask in F0-F4 function evaluation, Handle NULL-pointer in get_direction(), CMakelists.txt disable optimizing, Upload CLion config
    [core0.c]
2023-12-30 Revert changes to LOG macro
    [core0.c, core1.c]
2024-01-01 Reformatting and renaming some functions; replaced get_direction() with get_direction_of_speed_step() in order to simplify handling of direction; additional explanation comment in CV.h; add doxygen c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
    [core0.c, core1.c]
2024-01-02 Simplify get_speed_step_table_index_of_speed_step(); Removed unnecessary parameter from adjust_pwm_level function; Removed some redundant else statements and redundant "== true" from some expressions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
    [core0.c, core1.c]
2024-01-02 Refactor Motor PWM init and ADC init; Added doxygen documentation for some functions; Changed some settings in Doxyfile
2024-01-03 Replace '≙' with '='
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2024-01-09 Add note regarding U1 / PJ75AL33SA LDO / Issue 23 to schematic; Update KiCad Project to version 7; Change C16 and C17 to 10pF
    [RP2040-Decoder.kicad_pcb, RP2040-Decoder.kicad_sch]
2024-01-27 Replace PJ75AL33SA with HT7533S
    [RP2040-Decoder.kicad_pcb, RP2040-Decoder.kicad_sch]
2024-11-24 New 4-Layer Board with USB; Update gitignore; Change Speed Table Comment;
    [RP2040-Decoder.kicad_pcb, RP2040-Decoder.kicad_sch, USB4105-GF-A.stp]
2024-11-24 Add LCSC Part numbers
    [RP2040-Decoder.kicad_pcb, RP2040-Decoder.kicad_sch]
2024-11-24 Changed 'LCSC Part Number' Field to 'LCSC Part #'
    [RP2040-Decoder.kicad_pcb, RP2040-Decoder.kicad_sch]
2024-11-25 Moving some components on the schematic
    [RP2040-Decoder.kicad_pcb, RP2040-Decoder.kicad_sch]
2024-11-26 fix file extension and pcb path
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2024-12-22 Moved all software related files to Software folder; Now using flash safe execution functions of pico_flash (pico SDK) lib; Added error handling; Added RP2040-Decoder-board.h definition; Adapted CMak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
    [core0.c, core1.c]
2024-12-22 Expanded on stdio logging functionality, also configuration of logging is now entirely in CMakeLists.txt for convenience, also warns now for logging configurations that make no sense; Clarification i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
    [core0.c, core1.c]
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2024-12-25 Update Docs; Add 3D-Models for flash and Motor driver; Update Readme; Check program code for exceeding size in CMakeLists.txt; Moved measure() function to core1.c/core1.h; Added direction enum typede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
    [RP2040-Decoder.kicad_pcb, RP2040-Decoder.kicad_sch]
2024-12-29 - Updated CMakeLists.txt and board config .h files - Refactored core0.c to most functions are now static functions. - Introduced new structures (`dcc_packet_t` and `dcc_ring_buffer_t`) for DCC packet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
    [core0.c, core1.c]
2024-12-30 Put both HW revisions into subfolders of KiCad folder
    [RP2040-Decoder.kicad_pcb, RP2040-Decoder.kicad_sch]
2024-12-30 Update pcb_render.yml
    Fix wrong folder due to new subfolder for revisions
2024-12-31 Change C18 to be 0603 - 25V and rotate on PCB for easier soldering; Small logging changes; Speed step enums are actually used now for better clarity; Introduced cv_setup_check_done and flash_safe_exe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
    [RP2040-Decoder.kicad_pcb, RP2040-Decoder.kicad_sch]
2025-01-03 Replaced solder bridge with tactile button; Fixed Footprint Rotation in position file; Fixed .gitignore for production outputs
    [434133025816.stp, RP2040-Decoder.kicad_pcb, RP2040-Decoder.kicad_sch]
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2025-01-31 Update RP2040-Decoder.kicad_pcb
    This is my first time commenting.
    There are 6 locations with 0.2mm drill holes.
    I think 0.3mm is sufficient for these.
    This reduces manufacturing costs.
    Thank you for your consideration.
    [RP2040-Decoder.kicad_pcb]
2025-04-14 Change PCB to rev 1.1 to reflect changes in PR35 from @HMX-1972
    [RP2040-Decoder.kicad_sch]
2025-04-14 Rename Rev_1_0 KiCad folder to USB and Rev_0_3 folder to Legacy
    [434133025816.stp, RP2040-Decoder.kicad_pcb, RP2040-Decoder.kicad_sch]
2025-04-15 Update README and add Revision attribute to PCB which updates Rev x.x silkscreen on the back side;
    [RP2040-Decoder.kicad_pcb]
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2025-11-29 docs: Improve motor control documentation details and cross-references
    - Corrected Back-EMF measurement CV from CV63 to CV61.
    - Rewrote 'Startup Controller' section for clarity and accuracy.
    - Added Sphinx C cross-references for get_kp(), init_controller(), and speed_helper() functions.
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
